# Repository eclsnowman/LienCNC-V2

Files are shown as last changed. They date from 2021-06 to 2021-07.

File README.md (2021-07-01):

# LienCNC-V2
My Design for a Heavy Duty CNC Router

LienCNC V2 Render1

Hello and welcome to my Github for the LienCNC V2, which is a CNC router I designed as an upgrade to my previous CNC Router. I completed this new router design and build during December of 2020. The previous router I used was the R7 CNC which was a project I helped develop with my friend Brandon who owned SMW3D/HobbyFab. The R7 CNC was a great machine and cut all the aluminum parts required to build my new machine. The majority of the work I do on my router is cutting aluminum, so I wanted something with higher stiffness, higher mass for dampening vibrations, and all around overbuilt just how I like it.

The performance of this new machine checks all the boxes I had hoped for during my time in Solidworks designing the upgrade. The major specifications for this CNC design are as follows:

***Construction:*** 8020 Aluminum Profiles and ½” ATP-5 Cast tooling plates  
***Motion:*** RM1605 (5mm pitch) Ball Screws, HGR20 Linear Rails, Nema24 3Nm Closed Loop Steppers  
***Spindle:*** 2.2KW ER20 220V 24000RPM Spindle  
***Controls:*** Minisforum UM300 MiniPC into CNCDrive AXBB-E Controller w/ UCSB Breakout  
***Software:*** CNCDrive UCCNC 1.2113  
***Power Supplies:*** 48V/20A Main PSU, 24V/2.5A PSU, 5V10A PSU, 48V-to-12V 5A Buck Converter  
***Machine Travel:*** X=738mm  /  Y=724.5mm  /  Z=129mm  
***Max Speed:*** X=8,000mm/min  /  Y=10,000mm/min  /  Z = 8,000mm/min  

In the files I have on this Github are all my native Solidworks 2018 design files, as well as those files converted into many other 3D formats including; Fusion360, Step, Iges, Etc. In addition, I have included PDF, DXF, and DWG prints for all the major fabricated components and assemblies. The manuals for all the components that I referenced for configuring my build are also included. Lastly I have included my UCCNC configuration *.pro” file. 

The only item I have not included is a wiring diagram. Unfortunately the time it would take to make a wiring diagram to the caliber I could feel proud of is just not something I have time for right now. Building a CNC requires a fairly ample back catalog of knowledge to take on. If the wiring of a project like using the electrical manuals is not something you feel comfortable with, then seeking advice from an expert on your project would be advised. That being said I have included pictures and 3D models of my electrical cabinet design that you could use as reference on your own project.

I hope the files, resources, pictures, and designs I have provided here can help you if you decide to take on this project. And if you don’t build this design, I hope these resources can act as a jumping off point for your own project.

If you find any errors that I should correct please feel free to submit a pull request with the changes, or submit an issue and I will do my best to correct the problem as time allows.

Happy Making,
– Eric Lien

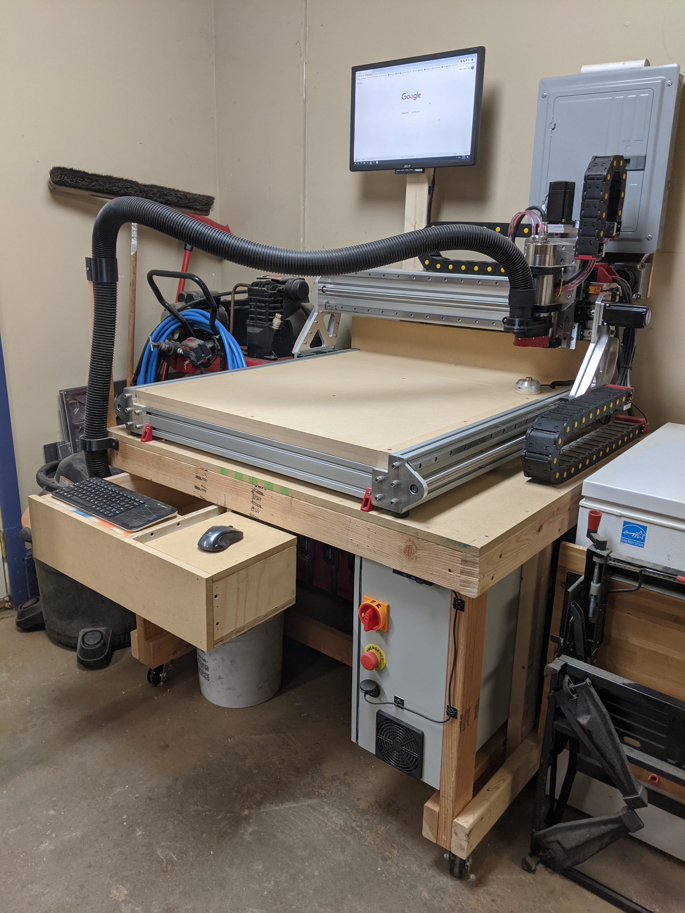
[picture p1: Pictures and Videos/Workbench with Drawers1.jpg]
LienCNC V2 Finished

LienCNC V2 Render2

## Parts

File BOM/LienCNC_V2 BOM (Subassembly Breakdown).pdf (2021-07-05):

LienCNC V2

ITEM NO.

QTY. By
| Assembly | PART NUMBER | DESCRIPTION | Prints & Manuals
1 | 1 | CNC Base and Electronics | Assembly | LCNC_BC & LCNC_TLA
1.1 | 1 | Workbench | Wood | LCNC_WB
1.1.1 | 1 | 2x4 Frame | Lumber Frame | LCNC_WB
1.1.1.1 | 654 in | 2x4 (Pine) | 2x4 Lumber (1.5" x 3.5") | LCNC_WB
1.1.2 | 1 | Workbench Lower Shelf | 3/4" Plywood or MDF | LCNC_WB
1.1.3 | 1 | Workbench Top | 3/4" Plywood or MDF | LCNC_WB
1.1.4 | 2 | 2406T34 | Ridged Caster | LCNC_WB
1.1.5 | 2 | 2406T29 | Swivel Caster | LCNC_WB
1.1.6 | 1 | Shelf Back Panel | 3/4" Plywood or MDF | LCNC_WB
1.1.7 | 16 | 92351A544 | 1/4" x 1-1/4"L Lag | LCNC_WB
1.2 | 1 | LienCNC_Base | CNC Base Frame | LCNC_BA
1.2.1 | 1 | 8020_Base_Frame | 8020 Aluminum Frame Components | LCNC_BF
1.2.1.1 | 2 | 40-4012 (1000mm) | 80/20 40-4012 PROFILE | LCNC_BF
1.2.1.2 | 4 | 40-4080 (860mm) | 80/20 40-4080 PROFILE | LCNC_BF
1.2.2 | 1 | Spoilboard (Bottom) | 3/4" MDF Bottom Spoilboard | LCNC_BA
1.2.3 | 1 | Spoilboard (Top) | 3/4" MDF Top Spoilboard | LCNC_BA
1.2.4 | 36 | 98689A116 | 8mm SST Washer | LCNC_BA
1.2.5 | 16 | 91292A208 | SCS M8 x 1.25 x 45mm Long PT (SST) | LCNC_BA
1.2.6 | 20 | 8mm SCS SST x 25mm | Stainless Steel M8 Socket Head Cap Screw | LCNC_BA
1.2.7 | 4 | 40-2849 (8020 Foot) | 8020 Rubber Foot | LCNC_BA
1.2.8 | 8 | 40-1984 | M8 Tnut for 40 series Tslot | LCNC_BA
1.2.9 | 16 | 5mm SCS SST x 12mm | M5 SCS | LCNC_BA
1.2.10 | 16 | 98689A114 | 5mm SST Washer | LCNC_BA
1.2.11 | 16 | M5_Tnut_40Series-Profile | M5 Tnut for 40 series Tslot | LCNC_BA
1.2.12 | 1 | Y_Axis_Endplate | Front Right Y Axis Endplate | LCNC_YE & LCNC_BA
1.2.13 | 2 | Nema24_Yaxis_Endplate | Fabricated Plate | LCNC_YE & LCNC_BA
1.2.14 | 2 | Backsplash | 1/8" Aluminum Dust Backsplash | LCNC_DG & LCNC_BA
1.2.15 | 2 | Side Profiles | Fabricated Angle Aluminum Side Dust Profiles | LCNC_DG & LCNC_BA
1.2.16 | 1 | MirrorY_Axis_Endplate | Fabricated Plate | LCNC_YE & LCNC_BA
1.3 | 1 | CNC Control Panel | Electrical CNC Controls | LCNC_CP & LCNC_BC
1.3.1 | 1 | YuCo YC-20X16X10-UL | 16x20x10 Yuco Electronics Enclosure | LCNC_CP
1.3.2 | 1 | SCN-1000-48 | 48V/20A Switching CNC Power supply | LCNC_CP
1.3.3 | 1 | MEAN WELL MDR 24V | MEAN WELL MDR-60-24 DIN-Rail Power Supply 24V 2.5 Amp 60W | LCNC_CP
1.3.4 | 1 | MEAN WELL MDR 5V | MEAN WELL MDR-60-5 AC to DC DIN-Rail Power Supply 5V 10 Amp 50W | LCNC_CP
1.3.5 | 1 | CNCDRIVE AXBB-E | AXBB-E Ethernet Motion Controller + UCCNC License File Bundle) | LCNC_CP
1.3.6 | 1 | CNCDIVE UCSB | UCSB single port breakout board for AXBB-E | LCNC_CP
1.3.7 | 1 | CNCDrive_Parts_Mount | 3D Printed Part | LCNC_CP & STLs
1.3.8 | 4 | CL57Y Stepper Driver | YE Series 1 Axis Closed Loop Stepper CNC Kit 3.0 Nm(424.92oz.in) Nema 24
| | | Motor & Driver | LCNC_CP
1.3.9 | 1 | 7578K262 | Slotted Wire Duct with Snap-on Cover Adhesive-Back, 2-1/4" Ht X 1-1/2" Wd, 3-
| | | 1/4'Lg, Gray | LCNC_CP
1.3.10 | 1 | 8961K150 | Steel DIN 3 Rail, 7.5mm Deep | LCNC_CP
1.3.14 | 2 | Lovato Electric FB01F1P | DIN Rail Mounted Midget Fuse Holder, 2 Pole, 18 to 8 AWG, 30 Amp, 600V | LCNC_CP
1.3.15 | 10 | 7641K526 | AKA 7641K52 = Screw Terminal DIN-Rail Terminal Block (8-22 ga) | LCNC_CP
1.3.16 | 2 | 7641K350 | Din Rail Mounted End Stop | LCNC_CP
1.3.17 | 4 | 7641K924 | AKA 7641K921 = Screw Terminal DIN-Rail Terminal Block (12-22 ga) | LCNC_CP
1.3.18 | 18 | M5 Bolt Nut Washer Assembly | Assembly | LCNC_CP
1.3.18.1 | 18 x 1 | 5mm x 12mm SST BSC | 5mm x 10mm SST BSC | LCNC_CP
1.3.18.2 | 18 x 1 | M5 Nylock Nut | Trimcraft M5 Nylock Nut | LCNC_CP
1.3.18.3 | 18 x 2 | M5 Flat Washer | Trimcraft M5 Flat Washer | LCNC_CP
1.3.19 | 1 | MinixForum_UM300 | Mini PC for running UCCNC | LCNC_CP
1.3.20 | 1 | Power Brick Mount | 3D Printed Part | LCNC_CP & STLs
1.3.21 | 1 | UM300 Power Brick | Part of UM300 | LCNC_CP
1.3.22 | 1 | 120mm Fan | 120mm (48V) fan | LCNC_CP
1.3.23 | 2 | 120mm Filter | 120mm filter for air inlet and outlet | LCNC_CP
1.3.24 | 1 | ALLEN-BRADLEY_194E-E25-1753-6N | Main Disconnect | LCNC_CP
1.3.25 | 1 | YW1B-V4E11R EMERGENCY STOP (IDEC) | Estop (one NO one NC contact) | LCNC_CP
1.3.26 | 1 | Gland Plate Assembly | Assembly | LCNC_CP
1.3.26.1 | 1 | Controller Gland Plate | Fabricated Plate | LCNC_CP
1.3.26.2 | 5 | GX20-4 Aviation Connector | 20mm 4 pin panel connection (Stepper Coils and 12V Power) | LCNC_CP
1.3.26.3 | 5 | GX12-3 Aviation Connector | 12mm 3 pin panel connection (Limit Switches and Tool Probe)) | LCNC_CP
1.3.26.4 | 4 | GX16-6 Aviation Connector | 20mm 4 pin panel connection (Encoder Connections) | LCNC_CP
1.3.26.5 | 2 | Female US 3 Pin Power Socket Plug Panel Mount | US 3 Pin Power Plugs for external VAC and Aux Plugs | LCNC_CP
1.3.26.6 | 1 | CNLINKO LP24 4pin Connector | 4 Pin Plug Disconnect for VFD Power to Spindle | LCNC_CP
1.3.26.7 | 1 | BATIGE USB3_HDMI_Panel_Mount | Panel mount HDMI out to Monitor | LCNC_CP
1.3.26.8 | 1 | 3/4 Knockout Cord Grip | 3/4" Knockout Cord Grip for Controller Power In | LCNC_CP
1.3.27 | 1 | IceSpring_USB3_X2_Panel_Mount | Panel Mount USB for Front Connection to Mini PC | LCNC_CP
1.3.28 | 1 | GT-2R2G-2 (220V) Huanyang VFD | HUANYANG - 2.2KW 220V AC Vector Control VFD With Modbus | LCNC_CP
1.3.29 | 1 | AD-SSR630-22-DCZ | 30A SSR Relay | LCNC_CP
1.3.30 | 1 | AD-SSR210-22-DCZ | 10A SSR Relay | LCNC_CP
1.4 | 4 | 92351A544 | 1/4" x 1-1/4"L Lag | LCNC_BC
1.5 | 4 | 92141A029 | 1/4" Flat Washer | LCNC_BC
2 | 1 | X Axis ASMB | Assembly | LCNC_XA & LCNC_TLA
2.1 | 1 | X Axis_Beam | Assembly | LCNC_XA
2.1.1 | 1 | 40-8016 (1000mm) | 80/20 40-8016 PROFILE | LCNC_XB & LCNC_XA
2.2 | 2 | HGR20 LINEAR GUIDE SUBASSEMBLY | Assembly | LCNC_XA
2.2.1 | 1 x 2 | HGR20R x 1000 mm | 20mm Linear Rail | LCNC_XA
2.2.2 | 2 x 2 | HGH20CAZ0C | 20mm Linear Rail Block | LCNC_XA
2.2.2.3 | 2 x 1 | 2421K31 | M6 x1 Low Profile Zerk | LCNC_XA
2.2.3 | 17 | M5_Rail_Mounting-Tnut_ASMB | Assembly | LCNC_XA
2.2.3.1 | 17 x 1 | 5mm SCS SST x 20mm | M5 SCS | LCNC_XA
2.2.3.2 | 17 x 1 | 98689A114 | M5 Compact Washer | LCNC_XA
2.2.3.3 | 17 x 1 | M5_Tnut_40Series-Profile | M5 Tnut for 40 series Tslot | LCNC_XA
2.3 | 1 | Endstop_With_Mount(X_Y) | Assembly | LCNC_XA
2.3.1 | 1 | Endstop Rail Mount | 3D Printed Part | LCNC_XA & STLs
2.3.2 | 1 | TL-W5MC1 | Inductive Probe(NO NPN) | LCNC_XA
2.3.3 | 2 | M3 SCS SST x 10mm | M3 SCS | LCNC_XA
2.4 | 1 | Spindle Cooling Radiator System | Assembly | LCNC_SR
2.4.1 | 1 | XSPC EX240 Radiator | 240mm Radiator | LCNC_SR
2.4.2 | 2 | Noctua_nf-p12 redux-1700 | 20mm Fan (12V) | LCNC_SR
2.4.3 | 1 | Freezemod FS6PD-17 Pump and Resevoive combo | Freezemod Pump/Reservoir | LCNC_SR

See print LCNC_OV for full assembly overview

2.4.3.2 | 1 | Freezemod PU-FS6M Bracket | Fabricated Plate | LCNC_DG & LCNC_SR
2.4.3.3 | 1 | Bitspower_T_Fitting | G14 T-Fitting | LCNC_SR
2.4.3.4 | 2 | EK-AF Extender Rotary M-M G1_4 | G14 MxM Swivel Union | LCNC_SR
2.4.3.5 | 2 | EK-AF Angled 90deg G1_4 | G14 MxF Swivel 90deg Elbow | LCNC_SR
2.4.3.6 | 2 | G14x6mm_Barb | G14 Male x 6mm Barb Fitting | LCNC_SR
2.4.3.7 | 1 | G14_Valve | Válvula Bitspower Roscas 1/4" | LCNC_SR
2.4.3.8 | 1 | G14_Plug | G14 Plug (Acetal) | LCNC_SR
2.4.4 | 2 | G14x6mm_Barb | G14 Male x 6mm Barb Fitting | LCNC_SR
2.4.5 | 1 | Flow_Temp_Indicator_ASMB | Assembly | LCNC_SR
2.4.5.1 | 1 | Flow and Temp Printed Mount | 3D Printed Part | LCNC_SR & STLs
2.4.5.2 | 1 | Fosa Pointer Temp Display | Digital Temp Indicator | LCNC_SR
2.4.5.3 | 1 | Fosa G14 Flow Meter | Acrylic Flow Wheel Indicator | LCNC_SR
2.4.5.4 | 1 | EK-AF Angled 90deg G1_4 | G14 MxF Swivel 90deg Elbow | LCNC_SR
2.4.5.5 | 2 | G14x6mm_Barb | G14 Male x 6mm Barb Fitting | LCNC_SR
2.4.6 | 1 | EK-AF Angled 90deg G1_4 | G14 MxF Swivel 90deg Elbow | LCNC_SR
2.4.7 | 1 | Water Cooling Tubes | 5mm ID x 8mm OD Clear Tube | LCNC_SR
2.4.8 | 2 | G14_Plug | G14 Plug (Acetal) | LCNC_SR
2.4.9 | 1 | Radiator Mount1 | 3D Printed Part | LCNC_SR & STLs
2.4.10 | 1 | Radiator Mount2 | 3D Printed Part | LCNC_SR & STLs
2.4.11 | 2 | Fan_Grill | 3D Printed Part | LCNC_SR & STLs
2.4.12 | 4 | 3mm x 06mm SST BSC | 3mm x 6mm SST BSC | LCNC_SR
2.4.13 | 8 | 3mm x 30mm SST BSC | 3mm x 30mm SST BSC | LCNC_SR
2.4.14 | 6 | 5mm SCS SST x 16mm | M5 SCS | LCNC_SR
2.4.15 | 8 | 98689A114 | 5mm SST Washer | LCNC_SR
2.4.16 | 8 | M5_Tnut_40Series-Profile | M5 Tnut for 40 series Tslot | LCNC_SR
2.4.17 | 2 | 5mm SCS SST x 25mm | M5 SCS | LCNC_SR
2.4.18 | 4 | 4mm SCS SST x 08mm | M4 SCS | LCNC_SR
2.4.19 | 4 | 98689A113 | 4mm SST Washer | LCNC_SR
2.5 | 1 | XandY Axis Ballscrew ASMB | Assembly | LCNC_XA
2.5.1 | 4 | 5mm SCS SST x 25mm | M5 SCS | LCNC_XA
2.5.2 | 10 | 98689A114 | 5mm SST Washer | LCNC_XA
2.5.3 | 4 | 91290A207 | M6 BO FT SCS x 60mm | LCNC_XA
2.5.4 | 4 | 98689A115 | 6mm SST Washer | LCNC_XA
2.5.5 | 1 | Nema24_Spacer_Plate | Fabricated Plate | LCNC_MP2 & LCNC_XA
2.5.6 | 1 | 24HE34-5004D-E1000 | Nema 24 - 3Nm CL Stepper | LCNC_XA
2.5.7 | 1 | SFU1605-1610_Ball-Nut-Housing | 16mm Ball Screw Nut Housing | LCNC_XA
2.5.8 | 1 | RM1605-C7 L1000_Overall | 16mm Ball Screw x 1000mm L | LCNC_XA
2.5.9 | 1 | SFU1605-3 | 16mm Ball Screw Nut | LCNC_XA
2.5.10 | 1 | BK12 | 12mm Fixed Side Bearing Block | LCNC_XA
2.5.11 | 1 | Shaft Coupling (3 piece) | 10mm x 10 mm Shaft Coupling | LCNC_XA
2.5.11.1 | 2 | 9939T321 | Set Screw Vibration-Damping Precision Flexible Shaft Couplings | LCNC_XA
2.5.11.2 | 1 | 9845T14 | Urethane Flex Shaft Spider | LCNC_XA
2.5.12 | 1 | 6661K83 | 6000-2RS (10x26x8 Sealed Bearing) | LCNC_XA
2.5.13 | 6 | 5mm x 20mm SST BSC | 5mm x 10mm SST BSC | LCNC_XA
3 | 1 | Y Axis ASMB | Assembly | LCNC_YR
3.1 | 1 | Gantry_Riser | Fabricated Plate | LCNC_GP1 & LCNC_YR
3.2 | 1 | Y-Axis_Ballscrew_Connection_Plate | Fabricated Plate | LCNC_MP2 & LCNC_YR
3.3 | 1 | Gantry Rib1 | Fabricated Plate | LCNC_GR & LCNC_YR
3.4 | 1 | Gantry Rib2 | Fabricated Plate | LCNC_GR & LCNC_YR
3.5 | 1 | Drag Chain Mount (Y Axis) | Fabricated Plate | LCNC_MP2 & LCNC_YR
3.6 | 1 | Endstop_With_Mount(X_Y) | Assembly | LCNC_YR
3.6.1 | 1 | Endstop Rail Mount | 3D Printed Part | LCNC_YR & STLs
3.6.2 | 1 | TL-W5MC1 | Inductive Probe(NO NPN) | LCNC_YR
3.6.3 | 2 | M3 SCS SST x 10mm | M3 SCS | LCNC_YR
3.7 | 1 | 91290A238 | 5mm BO SCS x 18mm | LCNC_YR
3.8 | 1 | 91828A241 | M5 Hex Nut | LCNC_YR
3.9 | 8 | M8 SCS SST x 30mm | M8 SCS | LCNC_YR
3.10 | 8 | 98689A116 | 8mm SST Washer | LCNC_YR
3.11 | 19 | 5mm SCS SST x 20mm | M5 SCS | LCNC_YR
3.12 | 27 | 98689A114 | 5mm SST Washer | LCNC_YR
3.13 | 4 | 5mm SCS SST x 25mm | M5 SCS | LCNC_YR
3.14 | 4 | 5mm SCS SST x 12mm | M5 SCS | LCNC_YR
3.15 | 1 | HGR20 LINEAR GUIDE SUBASSEMBLY | Assembly | LCNC_YR
3.15.1 | 1 | HGR20R x 1000 mm | 20mm Linear Rail | LCNC_YR
3.15.2 | 2 | HGH20CAZ0C | 20mm Linear Rail Block | LCNC_YR
3.15.2.3 | 1 | 2421K31 | M6 x1 Low Profile Zerk | LCNC_YR
3.15.3 | 17 | M5_Rail_Mounting-Tnut_ASMB | Assembly | LCNC_YR
3.15.3.1 | 17 x 1 | 5mm SCS SST x 20mm | M5 SCS | LCNC_YR
3.15.3.2 | 17 x 1 | 98689A114 | M5 Compact Washer | LCNC_YR
3.15.3.3 | 17 x 1 | M5_Tnut_40Series-Profile | M5 Tnut for 40 series Tslot | LCNC_YR
4 | 2 | XandY Axis Ballscrew ASMB | Assembly (2 x One for each Y Axis) | LCNC_YR
4.1 | 2 x 4 | 5mm SCS SST x 25mm | M5 SCS | LCNC_YR
4.2 | 2 x 10 | 98689A114 | 5mm SST Washer | LCNC_YR
4.3 | 2 x 4 | 91290A207 | M6 BO FT SCS x 60mm | LCNC_YR
4.4 | 2 x 4 | 98689A115 | 6mm SST Washer | LCNC_YR
4.5 | 2 x 1 | Nema24_Spacer_Plate | Fabricated Plate | LCNC_MP2 & LCNC_YR
4.6 | 2 x 1 | 24HE34-5004D-E1000 | Nema 24 - 3Nm CL Stepper | LCNC_YR
4.7 | 2 x 1 | SFU1605-1610_Ball-Nut-Housing | 16mm Ball Screw Nut Housing | LCNC_YR
4.8 | 2 x 1 | RM1605-C7 L1000_Overall | | LCNC_YR
4.9 | 2 x 1 | SFU1605-3 | 16mm Ball Screw Nut | LCNC_YR
4.10 | 2 x 1 | BK12 | 12mm Fixed Side Bearing Block | LCNC_YR
4.11 | 2 x 1 | Shaft Coupling (3 piece) | 10mm x 10 mm Shaft Coupling | LCNC_YR
4.11.1 | 2 x 2 | 9939T321 | Set Screw Vibration-Damping Precision Flexible Shaft Couplings | LCNC_XA
4.11.2 | 2 x 1 | 9845T14 | Urethane Flex Shaft Spider | LCNC_YR
4.12 | 2 x 1 | 6661K83 | 6000-2RS (10x26x8 Sealed Bearing) | LCNC_YR
4.13 | 2 x 6 | 5mm x 20mm SST BSC | 5mm x 10mm SST BSC | LCNC_YR
5 | 1 | Y Axis ASMB (Mirror) | Assembly | LCNC_YL
5.1 | 1 | Y-Axis_Ballscrew_Connection_Plate | Fabricated Plate | LCNC_MP2 & LCNC_YL
5.2 | 1 | Gantry Rib1 | Fabricated Plate | LCNC_GR & LCNC_YR
5.3 | 1 | Gantry Rib2 | Fabricated Plate | LCNC_GR & LCNC_YR
5.4 | 1 | MirrorGantry_Riser | Fabricated Plate | LCNC_GP2 & LCNC_YL
5.5 | 1 | Endstop_With_Mount(X_Y) | Assembly | LCNC_YL
5.5.1 | 1 | Endstop Rail Mount | 3D Printed Part | LCNC_YL & STLs
5.5.2 | 1 | TL-W5MC1 | Inductive Probe(NO NPN) | LCNC_YL

5.5.3 | 2 | M3 SCS SST x 10mm | M3 SCS | LCNC_YL
5.6 | 1 | 91290A238 | 5mm BO SCS x 18mm | LCNC_YL
5.7 | 1 | 91828A241 | M5 Hex Nut | LCNC_YL
5.8 | 8 | M8 SCS SST x 30mm | M8 SCS | LCNC_YL
5.9 | 8 | 98689A116 | 8mm SST Washer | LCNC_YL
5.1 | 16 | 5mm SCS SST x 20mm | M5 SCS | LCNC_YL
5.11 | 24 | 98689A114 | 5mm SST Washer | LCNC_YL
5.12 | 4 | 5mm SCS SST x 25mm | M5 SCS | LCNC_YL
5.13 | 4 | 5mm SCS SST x 12mm | M5 SCS | LCNC_YL
5.14 | 1 | HGR20 LINEAR GUIDE SUBASSEMBLY | Assembly | LCNC_YL
5.14.1 | 1 | HGR20R x 1000 mm | 20mm Linear Rail | LCNC_YL
5.14.2 | 2 | HGH20CAZ0C | 20mm Linear Rail Block | LCNC_YL
5.14.2.3 | 1 | 2421K31 | M6 x1 Low Profile Zerk | LCNC_YL
5.14.3 | 17 | M5_Rail_Mounting-Tnut_ASMB | Assembly | LCNC_YL
5.14.3.1 | 17 x 1 | 5mm SCS SST x 20mm | M5 SCS | LCNC_YL
5.14.3.2 | 17 x 1 | 98689A114 | M5 Compact Washer | LCNC_YL
5.14.3.3 | 17 x 1 | M5_Tnut_40Series-Profile | M5 Tnut for 40 series Tslot | LCNC_YL
6 | 1 | Z Axis ASMB | Assembly | LCNC_YL
6.1 | 1 | HY02D223B | 2.2KW - 24000RPM HUANYANG Spindle | LCNC_ZA & Huanyang 2.2KW Spindle.pdf
6.2 | 2 | YY-M-15 80mm | 80mm Spindle Clamp | LCNC_ZA
6.3 | 1 | Endmill | Endmill for representation purposes | LCNC_ZA
6.4 | 1 | TL-W5MC1 | Inductive Probe(NO NPN) | LCNC_ZA
6.5 | 1 | 24HE34-5004D-E1000 | Nema 24 - 3Nm CL Stepper | LCNC_ZA
6.6 | 1 | Banana Plug Socket (Black) | Black Z Probe Plug | LCNC_ZA
6.7 | 1 | Banana Plug Socket (Red) | Red Z Probe Plug | LCNC_ZA
6.8 | 2 | HGR20-300mm w/ 2xBlocks | 20mm x 300L Linear Rail w/ Bearings | LCNC_ZA
6.8.1 | 1 | HGR20R LINEAR GUIDE RAIL, CONFIGURABLE | 20mm Linear Rail | LCNC_ZA
6.8.2 | 2 | HGH20CAZ0C | 20mm Linear Rail Block | LCNC_ZA
6.8.2.3 | 1 | 2421K31 | M6 x1 Low Profile Zerk | LCNC_ZA
6.9 | 1 | BF12 | 12mm Support Side Bearing Block | LCNC_ZA
6.1 | 1 | BK12 | 12mm Fixed Side Bearing Block | LCNC_ZA
6.11 | 1 | RM1605-C7 L300_Overall | 16mm x 300mm Ballscrew | LCNC_ZA
6.12 | 1 | SFU1605-1610_Ball-Nut-Housing | 16mm Ball Screw Nut Housing | LCNC_ZA
6.13 | 1 | SFU1605-3 | 16mm Ball Screw Nut | LCNC_ZA
6.14 | 1 | Shaft Coupling (3 piece) | 10mm x 10 mm Shaft Coupling | LCNC_ZA
6.14.1 | 2 | 9939T321 | Set Screw Vibration-Damping Precision Flexible Shaft Couplings | LCNC_ZA
6.14.2 | 1 | 9845T14 | Urethane Flex Shaft Spider | LCNC_ZA
6.15 | 1 | Drag Chain Mount (Z Axis) | Fabricated Plate | LCNC_MP1 & LCNC_ZA
6.16 | 1 | Z_Axis_Motor_Plate | Fabricated Plate | LCNC_MP1 & LCNC_ZA
6.17 | 1 | Z_Axis_Plate | Fabricated Plate | LCNC_SP & LCNC_ZA
6.18 | 1 | Z_Axis_Spacer | Fabricated Plate | LCNC_MP1 & LCNC_ZA
6.19 | 1 | Z_Axis_Spacer_DC | Fabricated Plate | LCNC_MP2 & LCNC_ZA
6.2 | 1 | X_Axis_Plate | Fabricated Plate | LCNC_XP & LCNC_ZA
6.21 | 1 | X-Axis_Ballscrew_Connection_Plate | Fabricated Plate | LCNC_MP2 & LCNC_ZA
6.22 | 1 | Nema24_Spacer_Plate | Fabricated Plate | LCNC_MP2 & LCNC_ZA
6.23 | 1 | Drag Chain Mount (X Axis) | Fabricated Plate | LCNC_MP1 & LCNC_ZA
6.24 | 1 | Z_Axis_Endstop_Mount | 3D Printed Part | LCNC_ZA & STLs
6.25 | 1 | Spindle Probe Jack Mount | 3D Printed Part | LCNC_ZA & STLs
6.26 | 1 | 91290A238 | 5mm BO SCS x 18mm | LCNC_ZA
6.27 | 2 | 91828A241 | M5 Hex Nut | LCNC_ZA
6.28 | 26 | 5mm SCS SST x 25mm | M5 SCS | LCNC_ZA
6.29 | 81 | 98689A114 | 5mm SST Washer | LCNC_ZA
6.3 | 24 | 5mm SCS SST x 16mm | M5 SCS | LCNC_ZA
6.31 | 17 | 5mm SCS SST x 20mm | M5 SCS | LCNC_ZA
6.32 | 1 | 91290A194 | 5mm BO SCS x 30mm | LCNC_ZA
6.33 | 8 | 5mm SCS SST x 14mm | M5 SCS | LCNC_ZA
6.34 | 6 | M6 SCS BO PT x 40mm | 6mm BO PT SCS x 40mm | LCNC_ZA
6.35 | 6 | 98689A115 | 6mm SST Washer | LCNC_ZA
6.36 | 4 | 5mm SCS SST x 30mm | M5 SCS | LCNC_ZA
6.37 | 3 | 3mm x 10mm SST BSC | 3mm x 10mm SST BSC | LCNC_ZA
6.38 | 2 | 5mm x 10mm SST BSC | 5mm x 10mm SST BSC | LCNC_ZA
6.39 | 2 | 3mm x 16mm SST SCS | 3mm x 16mm SST SCS | LCNC_ZA
6.4 | 2 | 3mm x 12mm SST SCS | 3mm x 12mm SST SCS | LCNC_ZA
7 | 1 | X Axis Drag Chain ASMB | Assembly | LCNC_DC & LCNC_TLA
7.1 | 1 | Cable Chain X End Mount | 3D Printed Part | STLs
7.2 | 1 | Cable Chain Exit Combs V2 | 3D Printed Part | STLs
7.3 | 1 | Cable Chain Exit Combs | 3D Printed Part | STLs
7.4 | 1 | H25 (25x57mm Drag Chain) | Assembly | LCNC_DC
7.4.1 | 1 | H25-EndLink1 (25x57_ID_Drag_Chain) | Link1 | LCNC_DC
7.4.2 | 25 | H25-CenterLink (25x57_ID_Drag_Chain) | Link2 | LCNC_DC
7.4.3 | 1 | H25-EndLink2 (25x57_ID_Drag_Chain) | Link3 | LCNC_DC
7.5 | 8 | 5mm x 12mm SST BSC | 5mm x 10mm SST BSC | LCNC_DC
7.6 | 4 | 5mm x 10mm SST BSC | 5mm x 10mm SST BSC | LCNC_DC
7.7 | 6 | 5mm x 16mm SST BSC | 5mm x 10mm SST BSC | LCNC_DC
7.8 | 4 | 90225A101 | M5 Square Nut | LCNC_DC
7.9 | 2 | M5_Tnut_40Series-Profile | M5 Tnut for 40 series Tslot | LCNC_DC
7.1 | 2 | 98689A114 | 5mm SST Washer | LCNC_DC
8 | 1 | Z Axis Drag Chain ASMB | Assembly | LCNC_DC & LCNC_TLA
8.1 | 1 | H25 (25x38mm Drag Chain) | Assembly | LCNC_DC
8.1.1 | 1 | H25-EndLink1 (25x38_ID_Drag_Chain) | Link1 | LCNC_DC
8.1.2 | 10 | H25-CenterLink (25x38_ID_Drag_Chain) | Link2 | LCNC_DC
8.1.3 | 1 | H25-EndLink2 (25x38_ID_Drag_Chain) | Link3 | LCNC_DC
8.2 | 1 | Cable Chain Exit Combs Z1 | 3D Printed Part | STLs
8.3 | 1 | Cable Chain Exit Combs Z1 | 3D Printed Part | STLs
8.4 | 8 | 5mm x 16mm SST BSC | 5mm x 10mm SST BSC | LCNC_DC
8.5 | 8 | 90225A101 | M5 Square Nut | LCNC_DC
8.6 | 8 | 5mm x 12mm SST BSC | 5mm x 10mm SST BSC | LCNC_DC
9 | 1 | Y Axis Dragchain | Assembly | LCNC_DC & LCNC_TLA
9.1 | 1 | Cable Chain Exit Comb Y Exit V3 | 3D Printed Part | STLs
9.2 | 1 | Cable Chain X End Mount | 3D Printed Part | STLs
9.3 | 1 | Cable Chain Exit Comb Y Exit | 3D Printed Part | STLs
9.4 | 1 | H25 (25x57mm Drag Chain) | Assembly | LCNC_DC
9.4.1 | 1 | H25-EndLink1 (25x57_ID_Drag_Chain) | Link1 | LCNC_DC
9.4.2 | 25 | H25-CenterLink (25x57_ID_Drag_Chain) | Link2 | LCNC_DC

9.4.3

| 1 | H25-EndLink2 (25x57_ID_Drag_Chain) | Link3 | LCNC_DC
9.5 | 4 | 90225A101 | M5 Square Nut | LCNC_DC
9.6 | 4 | 5mm x 20mm SST BSC | 5mm x 10mm SST BSC | LCNC_DC
9.7 | 8 | 5mm x 12mm SST BSC | 5mm x 10mm SST BSC | LCNC_DC
9.8 | 4 | 5mm x 10mm SST BSC | 5mm x 10mm SST BSC | LCNC_DC
9.9 | 2 | 90305A112 | Wood Screw | LCNC_DC
10 | 1 | Dust_Shoe | Assembly | LCNC_DU
10.1 | 1 | Dust_Shoe | 3D Printed Part | LCNC_DU & STLs
10.2 | 8 | 3mm x 06mm SST BSC | 3mm x 6mm SST BSC | LCNC_DU
10.3 | 2 | 5mm SCS SST x 20mm | M5 SCS | LCNC_DU
10.4 | 2 | 98689A114 | 5mm SST Washer | LCNC_DU
10.5 | 2 | M5 Nylock Nut | Trimcraft M5 Nylock Nut | LCNC_DU
10.6 | 20 | 8mm x 3mm Neodymium Magnet | Magnets to hold on dust shoe | LCNC_DU
11 | 1 | 5Gallon_Pail_Dust_Cyclone | Assembly | LCNC_DU
11.1 | 1 | 5_Gallon_Pail | Cut down 5gal pail to act as upper section | LCNC_DU
11.2 | 1 | 5_Gallon_Pail | 5gal pail | LCNC_DU
11.3 | 1 | Cyclone_Top_Under_Plate | Fabricated Wood Plate | LCNC_DU
11.4 | 1 | 2in x 6in Length of PVC Pipe | 6in Length of PVC Pipe | LCNC_DU
11.5 | 2 | 4880K26 | 2in PVC FxF Elbow | LCNC_DU
11.6 | 1 | 2in x 1.75in Length of PVC Pipe | 1.75in Length of PVC Pipe | LCNC_DU
11.7 | 1 | 1608T103 | 2in PVC FxF Union | LCNC_DU
11.8 | 2 | 2IN_ABS_Coupling | 2IN_ABS_Coupling | LCNC_DU
11.9 | 1 | 1608T125 | 2in PVC FxF Elbow | LCNC_DU
11.1 | 1 | Cyclone_Baffle_Plate | Fabricated Wood Plate | LCNC_DU
11.11 | 4 | 90630A121 | 3/8" Nylock Nut | LCNC_DU
11.12 | 4 | 98023A031 | 3/8" Washer | LCNC_DU
11.13 | 1 | 95475A646 | 3/8 Threaded Rod | LCNC_DU
11.14 | 2 | 2IN_Pipe_to_2.25ID_Hose_Adapter | 3D Printed Part | LCNC_DU & STLs

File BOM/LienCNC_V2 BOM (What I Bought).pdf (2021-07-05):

LienCNC V2 Parts List | *Note, these are the parts I purchased. There are other items I had that other users might need to buy misc metric hardware, crimp wire ferruls, metric taps, misc interconnection wiring in control panel, etc.
Vendor | Qty: | PN / EAN# / ASIN# | Price (Ea) | Price (Total) | Description | Notes | Link
Amazon | 1 | HGR20-300 | $78.00 | $78.00 | Linear Guide Rail 2Pcs HGR20-300mm, Linear Slide Rail with 1Pcs RM1605-300mm Ballscrew with BF12/BK12 Kit Linear Slide Rail Guide Rail Square for DIY CNC Routers Lathes Mills | Note, my rail lengths were slightly over sized and ball screws were slightly off print. So I had to machine relief pockets in my plates for oversided rails and made 3DP spacers at the end of the ball screws to go between 6900-RS bearings and ball screw shoulders. | https://www.amazon.com/gp/product/B083CKZR5K/ref=ppx_y

o_dt_b_asin_title_o02_s00?ie=UTF8&psc=1 (https://www.amazon.com/gp/product/B083CKZR5K/ref=ppx_yo_dt_b_asin_title_o02_s00?ie=UTF8&psc=1)

Amazon | 3 | HGR20-1000 | $107.99 | $323.97

Linear Guide Rail 2Pcs HGR20-1000mm Linear Slide Rail with 1Pcs RM1605-1000mm Ballscrew with BF12/BK12 Kit Linear Slide Rail Guide Rail Square for DIY CNC Routers Lathes Mills. Note that since the design only uses 1 leanr rail per Y axis, you could just buy a seperate matching ball screw which means you only need 2 of these kits. But I didn't want any mismatch on the components, so now I just have 2 extra rails and 4 extra carriages as future spares.

Note, my rail lengths were slightly over sized and ball screws were slightly off
print. So I had to machine relief pockets in my plates for oversided rails and
made 3DP spacers at the
end of the ball screws to go between 6900-RS bearings
and ball screw shoulders.

https://www.amazon.com/gp/product/B083CKZR5K/ref=ppx_yo_dt_b_asin_title_o02_s00?ie=UTF8&psc=1 (https://www.amazon.com/gp/product/B083CKZR5K/ref=ppx_yo_dt_b_asin_title_o02_s00?ie=UTF8&psc=1)

Amazon | 1 | MDR-60-24 | $19.99 | $19.99 | MEAN WELL MDR-60-24 DIN-Rail Power Supply 24V 2.5 Amp 60W

https://www.amazon.com/gp/product/B005T6OBFU/ref=ppx_yo_dt_b_asin_title_o01_s00?ie=UTF8&psc=1 (https://www.amazon.com/gp/product/B005T6OBFU/ref=ppx_yo_dt_b_asin_title_o01_s00?ie=UTF8&psc=1)
Amazon | 1 | MDR-60-5 | $21.47 | $21.47 | MEAN WELL MDR-60-5 AC to DC DIN-Rail Power Supply 5V 10 Amp 50W | https://www.amazon.com/gp/product/B005T6SAJI/ref=ppx_yo_dt_b_asin_title_o01_s01?ie=UTF8&psc=1 (https://www.amazon.com/gp/product/B005T6SAJI/ref=ppx_yo_dt_b_asin_title_o01_s01?ie=UTF8&psc=1)
Amazon | 2 | BE-032-3-fba | $12.99 | $25.98 | 2PCS 10mm to 10mm Aluminium Plum Flexible Shaft Coupling Diameter 20mm Length 25mm Connector Flexible Coupler for 3D Printer CNC Machine and Servo Stepped Motor（10x10mm） | https://www.amazon.com/gp/product/B07TF63R4C/ref=ppx_yo_dt_b_asin_title_o01_s01?ie=UTF8&psc=1 (https://www.amazon.com/gp/product/B07TF63R4C/ref=ppx_yo_dt_b_asin_title_o01_s01?ie=UTF8&psc=1)
Amazon | 1 | EAN# 0737123111343 | $35.89 | $35.89 | DIN Rail Terminal Block Kit #2 Red/Black Dinkle 20 DK4N 10 AWG Gauge 30A 600V Ground DK4N-PE Jumper DSS4N-10P End Covers End Brackets | https://www.amazon.com/gp/product/B07NVVBY98/ref=ppx_y
o_dt_b_asin_title_o09_s08?ie=UTF8&psc=1 (https://www.amazon.com/gp/product/B07NVVBY98/ref=ppx_yo_dt_b_asin_title_o09_s08?ie=UTF8&psc=1)
Amazon | 1 | AFB01F2P | $18.99 | $18.99 | Automation Systems Interconnect ASI AFB01F2P DIN Rail Mounted Midget Fuse Holder, 2 Pole, 10 x 38 mm, 13/32" Diameter x 1.5" Length, 18 to 8 AWG, 30 Amp, 600V | https://www.amazon.com/gp/product/B00W4XV1XQ/ref=ppx_yo_dt_b_asin_title_o09_s08?ie=UTF8&psc=1 (https://www.amazon.com/gp/product/B00W4XV1XQ/ref=ppx_yo_dt_b_asin_title_o09_s08?ie=UTF8&psc=1)
Amazon | 1 | GLD11-40 (EAN# 0791294549923) | $18.99 | $18.99 | Electrical Buddy Universal Switch 2 Position 3 Phase Panel Rotary Selector Changeover Switch GLD11 40A AC 690V 40A | https://www.amazon.com/gp/product/B07TJW9V1V/ref=ppx_y
o_dt_b_asin_title_o09_s08?ie=UTF8&psc=1 (https://www.amazon.com/gp/product/B07TJW9V1V/ref=ppx_yo_dt_b_asin_title_o09_s08?ie=UTF8&psc=1)
Amazon | 1 | Batige - USBHDMI | $10.99 | $10.99

BATIGE USB 3.0 & HDMI to HDMI + USB3.0 AUX Extension Dash Panel Waterproof Car Flush Mount Cable for Car Boat and Motorcycle - 3ft https://www.amazon.com/gp/product/B073HZ4STM/ref=ppx_yo_dt_b_asin_title_o09_s07?ie=UTF8&psc=1 (https://www.amazon.com/gp/product/B073HZ4STM/ref=ppx_yo_dt_b_asin_title_o09_s07?ie=UTF8&psc=1)
Amazon | 1 | ASIN# B07VYWW2HG | $24.99 | $24.99 | CNLINKO LP24 Aviation Connector M24 Male Plug with Female Socket Waterproof Metal Thread Panel Connector 4 Pins for AC DC Signal LED Lighting Equipment | https://www.amazon.com/gp/product/B07VYWW2HG/ref=ppx_yo_dt_b_asin_title_o09_s06?ie=UTF8&psc=1 (https://www.amazon.com/gp/product/B07VYWW2HG/ref=ppx_yo_dt_b_asin_title_o09_s06?ie=UTF8&psc=1)
Amazon | 1 | ASIN# B07GZBXGR7 | $7.99 | $7.99 | 5PCS GX16-6, 6Pins, 16mm, Panel Metal Mount Circular Metal Aviation Connector Adapter Male Female Plug Socket (5 Pcs Set) | https://www.amazon.com/gp/product/B07GZBXGR7/ref=ppx_yo_dt_b_asin_title_o09_s05?ie=UTF8&psc=1 (https://www.amazon.com/gp/product/B07GZBXGR7/ref=ppx_yo_dt_b_asin_title_o09_s05?ie=UTF8&psc=1)
Amazon | 1 | ASIN# B0753FF184 | $22.99 | $22.99 | 5PCS GX20-4, 4Pins, 20mm, Panel Metal Mount Circular Metal Aviation Connector Adapter Male Female Plug Socket (5 Pcs Set) | https://www.amazon.com/gp/product/B0753FF184/ref=ppx_yo_dt_b_asin_title_o09_s03?ie=UTF8&psc=1 (https://www.amazon.com/gp/product/B0753FF184/ref=ppx_yo_dt_b_asin_title_o09_s03?ie=UTF8&psc=1)
Amazon | 1 | ASIN# B08H8JM451 | $9.99 | $9.99 | RJ45 Shielded Industrial Dual Panel Mount Female to Female Coupler Panel Mount Waterproof Connector Combo with Cap Network Connectors Cat5/5e/6 8P8C Connector Waterproof Cover (2 Pack, Black) | https://www.amazon.com/gp/product/B08H8JM451/ref=ppx_yo_dt_b_asin_title_o09_s03?ie=UTF8&psc=1 (https://www.amazon.com/gp/product/B08H8JM451/ref=ppx_yo_dt_b_asin_title_o09_s03?ie=UTF8&psc=1)
Amazon | 1 | ASIN# B078S17FZ5 | $8.00 | $8.00 | 10Pcs Black US 3 Pins Power Socket Plug Panel Screw Mount Type Female Connectors Adapter | https://www.amazon.com/gp/product/B078S17FZ5/ref=ppx_yo_dt_b_asin_title_o09_s03?ie=UTF8&psc=1 (https://www.amazon.com/gp/product/B078S17FZ5/ref=ppx_yo_dt_b_asin_title_o09_s03?ie=UTF8&psc=1)
Amazon | 1 | ASIN# B088FX3S8J | $5.81 | $5.81 | USB to RS485 Converter Adapter CH340T Chip 64-bit Suitable for Windows 7 8 10 (Pack of 2) | https://www.amazon.com/gp/product/B088FX3S8J/ref=ppx_yo_dt_b_asin_title_o09_s01?ie=UTF8&psc=1 (https://www.amazon.com/gp/product/B088FX3S8J/ref=ppx_yo_dt_b_asin_title_o09_s01?ie=UTF8&psc=1)
Amazon | 1 | E5-9JOT-1VXO | $12.99 | $12.99 | TWTADE/Red Mushroom Cap 1NO 1NC DPST Emergency Stop Push Button Switch AC 660V 10A (Quality Assurance for 3 Years) YW1B-V4E11R | https://www.amazon.com/gp/product/B07C2NJN94/ref=ppx_yo_dt_b_asin_title_o09_s01?ie=UTF8&psc=1 (https://www.amazon.com/gp/product/B07C2NJN94/ref=ppx_yo_dt_b_asin_title_o09_s01?ie=UTF8&psc=1)

*** Note: There are multiple tabs to this BOM. This page is what I expressly bought when I built it and the prices I paid. The next tab is a solidworks geberated BOM with every part in the assembly called out by assembly QTY.

Amazon | 1 | ASIN# B06XRT2YFV | $15.99 | $15.99

5PCS GX12-3, 3Pins, 12mm, Panel Metal Mount Circular Metal Aviation Connector Adapter Male Female Plug Socket (5 Pcs Set) https://www.amazon.com/gp/product/B06XRT2YFV/ref=ppx_yo_dt_b_asin_title_o09_s00?ie=UTF8&psc=1 (https://www.amazon.com/gp/product/B06XRT2YFV/ref=ppx_yo_dt_b_asin_title_o09_s00?ie=UTF8&psc=1)
Amazon | 1 | ASIN# B07TT4HH5L | $18.99 | $18.99 | 1238 48V Fan, 120mm x 38mm Dual Ball Bearings DC Brushless Cooling Fan | https://www.amazon.com/gp/product/B07TT4HH5L/ref=ppx_yo_dt_b_asin_title_o08_s01?ie=UTF8&psc=1 (https://www.amazon.com/gp/product/B07TT4HH5L/ref=ppx_yo_dt_b_asin_title_o08_s01?ie=UTF8&psc=1)
Amazon | 1 | ASIN# B075Q55ZNN | $9.99 | $9.99 | 120mm Fan Filter 2 Pack IP40 Dustproof Blower Guard ABS Computer Ventilator Grill 12cm Fan Mesh Cover Tool-Free Fan Strainer Compatible for 120x120 Case Fan USB Cooling Fan | https://www.amazon.com/gp/product/B075Q55ZNN/ref=ppx_y

o_dt_b_asin_title_o08_s00?ie=UTF8&psc=1 (https://www.amazon.com/gp/product/B075Q55ZNN/ref=ppx_yo_dt_b_asin_title_o08_s00?ie=UTF8&psc=1)
Amazon | 3 | ASIN# B07HBT3442 | $16.99 | $50.97 | R55 1M Length Plastic Closed can Open Cable Drag Chain Wire Carrier (25x57mm) | https://www.amazon.com/gp/product/B07HBT3442/ref=ppx_yo_dt_b_asin_title_o07_s01?ie=UTF8&psc=1 (https://www.amazon.com/gp/product/B07HBT3442/ref=ppx_yo_dt_b_asin_title_o07_s01?ie=UTF8&psc=1)
Amazon | 1 | ASIN# B077Z1W2HJ | $36.00 | $36.00 | Wokesi 14Pcs,ER20 1mm 2mm 3mm 4mm 5mm 6mm 7mm 8mm 9mm 10mm 11mm 12mm 13mm 1/8 Clamping Diameter,Spring Collet Chuck Set For CNC Lathe Machine Mill Tool(COLLET DIA:1mm-13mm T.I.R:8um,ER20) | https://www.amazon.com/gp/product/B077Z1W2HJ/ref=ppx_y

o_dt_b_asin_title_o06_s01?ie=UTF8&psc=1 (https://www.amazon.com/gp/product/B077Z1W2HJ/ref=ppx_yo_dt_b_asin_title_o06_s01?ie=UTF8&psc=1)
Amazon | 1 | EAN# 0753922958088 | $28.49 | $28.49 | CNC Spoilboard Surfacing Router Bits, 1/2 inch Shank 2 inch Cutting Diameter, Slab Flattening Router Bit Planing Bit Wood Milling Cutter Planer Woodworking Tool by NITOMAK (Carbide) | https://www.amazon.com/gp/product/B07WQG85HV/ref=ppx_yo_dt_b_asin_title_o05_s00?ie=UTF8&psc=1 (https://www.amazon.com/gp/product/B07WQG85HV/ref=ppx_yo_dt_b_asin_title_o05_s00?ie=UTF8&psc=1)
Amazon | 2 | ASIN# B07V4PR84Y | $10.99 | $21.98 | 3Pcs TL-W5MC1 5mm 3 Wire Inductive Proximity Sensor Detection Switch NPN DC 6-36V | https://www.amazon.com/gp/product/B07V4PR84Y/ref=ppx_yo_dt_b_asin_title_o03_s00?ie=UTF8&psc=1 (https://www.amazon.com/gp/product/B07V4PR84Y/ref=ppx_yo_dt_b_asin_title_o03_s00?ie=UTF8&psc=1)
Amazon | 1 | ASIN# B08514H2BJ | $27.00 | $27.00 | 5pcs ER20 Nut for Clamping collets, Balanced to G2.5/25000rpm-NUT-ER20-G25-New | https://www.amazon.com/gp/product/B08514H2BJ/ref=ppx_yo_dt_b_asin_title_o02_s00?ie=UTF8&psc=1 (https://www.amazon.com/gp/product/B08514H2BJ/ref=ppx_yo_dt_b_asin_title_o02_s00?ie=UTF8&psc=1)
Amazon | 1 | YC-ENC-FE-S YC-20X16X10-UL-FE | $196.00 | $196.00 | Yuco YC-20X16X10-UL-FE Fully Enclosed (no gland plate) IP66 Enclosure, UL Certified, Nema 4, 16 Gauge, Single Door Hinge Cover, Wall-Mount, Backplate (20 x 16 x 10) | https://www.amazon.com/gp/product/B074XGTHCK/ref=ppx_yo_dt_b_asin_title_o01_s00?ie=UTF8&psc=1 (https://www.amazon.com/gp/product/B074XGTHCK/ref=ppx_yo_dt_b_asin_title_o01_s00?ie=UTF8&psc=1)
Amazon | 1 | ASIN# B07RXK96GV | $4.99 | $4.99 | 10 Pcs FC-26P 2x13 Pin 2.54mm Dual Rows Female Header IDC Cable Connector | https://www.amazon.com/gp/product/B07RXK96GV/ref=ppx_yo_dt_b_asin_title_o00_s00?ie=UTF8&psc=1 (https://www.amazon.com/gp/product/B07RXK96GV/ref=ppx_yo_dt_b_asin_title_o00_s00?ie=UTF8&psc=1)
Amazon | 1 | ASIN# B07P9GM8H1 | $9.99 | $9.99 | 10Ft/3M IDC 26P 1.27mm Rainbow Color Flat Ribbon Wire | https://www.amazon.com/gp/product/B07P9GM8H1/ref=ppx_yo_dt_b_asin_title_o09_s00?ie=UTF8&psc=1 (https://www.amazon.com/gp/product/B07P9GM8H1/ref=ppx_yo_dt_b_asin_title_o09_s00?ie=UTF8&psc=1)
Amazon | 1 | EAN# 0713072774679 | $10.59 | $10.59 | 10 Pcs 6000-2RS Double Rubber Seal Bearings 10x26x8mm, Pre-Lubricated and Stable Performance and Cost Effective, Deep Groove Ball Bearings. | https://www.amazon.com/gp/product/B072F6J3GN/ref=ppx_yo_dt_b_asin_title_o08_s00?ie=UTF8&psc=1 (https://www.amazon.com/gp/product/B072F6J3GN/ref=ppx_yo_dt_b_asin_title_o08_s00?ie=UTF8&psc=1)
Amazon | 7 | ASIN# B07L11S1Q4 | $9.89 | $69.23 | Slide in T-Nut, M5 Threaded for 4040 Series Aluminum Extrusions Profile, Pack of 12 | https://www.amazon.com/gp/product/B07L11S1Q4/ref=ppx_yo_dt_b_asin_title_o07_s01?ie=UTF8&psc=1 (https://www.amazon.com/gp/product/B07L11S1Q4/ref=ppx_yo_dt_b_asin_title_o07_s01?ie=UTF8&psc=1)
Amazon | 1 | ASIN# B01LZA04NX | $41.49 | $41.49 | R55 25mm x 38mm Plastic Cable Wire Carrier Drag Chain 1M Black for CNC | https://www.amazon.com/uxcell-Plastic-Cable-Carrier-Chain/dp/B01LZA04NX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 (https://www.amazon.com/uxcell-Plastic-Cable-Carrier-Chain/dp/B01LZA04NX?s=industrial)
Amazon | 1 | EAN# 0737123110988 | $29.99 | $29.99 | Dinkle DIN Rail Block Kit #2 DIN Rail Terminal Block Kit Dinkle 20 DK4N 10 AWG Gauge Ground DK4N-PE Jumper DSS4N-10P End Covers End Brackets,30 Amp, 600V | https://www.amazon.com/gp/product/B01IDL6OW0/ref=ppx_yo_dt_b_asin_title_o05_s00?ie=UTF8&psc=1 (https://www.amazon.com/gp/product/B01IDL6OW0/ref=ppx_yo_dt_b_asin_title_o05_s00?ie=UTF8&psc=1)
Amazon | 1 | EAN# 0737123111329 | $28.99 | $28.99 | Dinkle UL Every Color DIN Rail Terminal Block Kit 20 DK2.5N 12 AWG Gauge 20A 600V Ground DK4N-PE Jumper DSS2.5N-10P End Covers End Brackets | https://www.amazon.com/gp/product/B07NVV28D9/ref=ppx_y
o_dt_b_asin_title_o05_s00?ie=UTF8&psc=1 (https://www.amazon.com/gp/product/B07NVV28D9/ref=ppx_yo_dt_b_asin_title_o05_s00?ie=UTF8&psc=1)
Amazon | 1 | 43235-27956 | $11.50 | $11.50 | 2 Ports Dual USB 3.0 Male to USB 3.0 Female AUX Flush Mount Car Mount Extension Cable for Car Truck Boat Motorcycle Dashboard Panel -(3 Feet) | | https://www.amazon.com/gp/product/B01MY1WDIU/ref=ppx_yo_dt_b_asin_title_o04_s00?ie=UTF8&psc=1 (https://www.amazon.com/gp/product/B01MY1WDIU/ref=ppx_yo_dt_b_asin_title_o04_s00?ie=UTF8&psc=1)
Amazon | 1 | 2KTK20 | $10.99 | $10.99 | KTK-20 Fast Acting Limitron Fuse 600 VAC 20A (2 Pack) QSU | | https://www.amazon.com/gp/product/B07VH8RDLV/ref=ppx_yo_dt_b_asin_title_o01_s01?ie=UTF8&psc=1 (https://www.amazon.com/gp/product/B07VH8RDLV/ref=ppx_yo_dt_b_asin_title_o01_s01?ie=UTF8&psc=1)
Amazon | 1 | EAN# 0712994005847 | $13.99 | $13.99 | Rocaris 5 Pcs M3 M4 M5 M6 M8 Titanium Coated HSS Spiral Flute Metric Taps Set | | https://www.amazon.com/gp/product/B01JSAFB92/ref=ppx_yo_dt_b_asin_title_o00_s01?ie=UTF8&psc=1 (https://www.amazon.com/gp/product/B01JSAFB92/ref=ppx_yo_dt_b_asin_title_o00_s01?ie=UTF8&psc=1)
Amazon | 1 | A03-DDK01-S-KH | $33.99 | $33.99 | Kehuashina CNC Z-Axis Router Mill Touch Plate Mach3 Tool Setting Probe Milling Tools Silver | | https://www.amazon.com/gp/product/B07FLQRKPN/ref=ppx_yo_dt_b_asin_title_o05_s00?ie=UTF8&psc=1 (https://www.amazon.com/gp/product/B07FLQRKPN/ref=ppx_yo_dt_b_asin_title_o05_s00?ie=UTF8&psc=1)
Amazon | 1 | ASIN# B08FDGJMVF | $399.90 | $399.90 | Minisforum - UM300 Mini PC AMD Ryzen 3 3300U Windows 10 Pro Mini PC Desktop Computer, Radeon Vega 6 Graphics,8GB DDR4 256GB SSD,HDMI2.0/DP/USB-C Triple 4K@60Hz Output,with1000M LAN Intel WIFI6 AX200 BT5.1 | | https://www.amazon.com/gp/product/B08FDGJMVF/ref=ppx_yo_dt_b_asin_title_o01_s00?ie=UTF8&psc=1 (https://www.amazon.com/gp/product/B08FDGJMVF/ref=ppx_yo_dt_b_asin_title_o01_s00?ie=UTF8&psc=1)
Amazon | 1 | ASIN# B01HOM9IZ4 | $26.99 | $26.99 | TEAMGROUP Elite 8GB Single DDR4 2400MHz PC4-19200 CL16 Unbuffered Non-ECC 1.2V SODIMM 260-Pin Laptop Notebook PC Computer Memory Module Ram Upgrade -TED48G2400C16-S01 - (1x 8GB) Single | | https://www.amazon.com/gp/product/B01HOM9IZ4/ref=ppx_yo_dt_b_asin_title_o01_s00?ie=UTF8&psc=1 (https://www.amazon.com/gp/product/B01HOM9IZ4/ref=ppx_yo_dt_b_asin_title_o01_s00?ie=UTF8&psc=1)
Amazon | 1 | ASIN# B07LD1HPYC | $13.99 | $13.99 | Beduan 8mm x 5mm Clear Pneumatic Tubing Pipe PU Polyurethane Air Compressor Tubing Hose Pipe Line Fluid Transfer 39.4ft 12 Meter | | https://www.amazon.com/gp/product/B07LD1HPYC/ref=ppx_yo_dt_b_asin_title_o00_s01?ie=UTF8&psc=1 (https://www.amazon.com/gp/product/B07LD1HPYC/ref=ppx_yo_dt_b_asin_title_o00_s01?ie=UTF8&psc=1)
Amazon | 1 | ASIN# B07D9JKT91 | $14.99 | $14.99 | fosa G1/4 Threaded Computer Water Cooling System Flow Meter Indicator Acrylic Replacement for PC Computer … | Need to wire pump at 12V (100% duty cycle) for this to function | https://www.amazon.com/gp/product/B07D9JKT91/ref=ppx_yo_dt_b_asin_title_o00_s01?ie=UTF8&psc=1 (https://www.amazon.com/gp/product/B07D9JKT91/ref=ppx_yo_dt_b_asin_title_o00_s01?ie=UTF8&psc=1)
Amazon | 1 | TBJ4812B60Z | $16.98 | $16.98 | DC Voltage Regulator Buck Converter DC 48V Step Down to 12V 5A 60W Reducer Power Converter Waterproof Module Transformer for Golf Cart Club Car | Mounted in bottom of control cabinet | https://www.amazon.com/gp/product/B07V8J6BJQ/ref=ppx_yo_dt_b_asin_title_o00_s01?ie=UTF8&psc=1 (https://www.amazon.com/gp/product/B07V8J6BJQ/ref=ppx_yo_dt_b_asin_title_o00_s01?ie=UTF8&psc=1)
Amazon | 1 | ASIN# B07QYFKCJB | $11.79 | $11.79 | fosa Pointer Display Thermometer with Waterproof Probe, PC G1/4 Thread Water Cooling System Temperature Meter for Computer Laptop | This can be wired at 12V or 5V | https://www.amazon.com/gp/product/B07QYFKCJB/ref=ppx_yo_dt_b_asin_title_o00_s01?ie=UTF8&psc=1 (https://www.amazon.com/gp/product/B07QYFKCJB/ref=ppx_yo_dt_b_asin_title_o00_s01?ie=UTF8&psc=1)

Amazon | 1 | ASIN# B07GS3JPW1 | $11.39 | $11.39 | Aramox 6 PCS Barb-Fitting, PC Water Cooling Two-Touch Fitting G1/4 Thread Barb Connector for Tube (6mm) | | https://www.amazon.com/gp/product/B07GS3JPW1/ref=ppx_od_dt_b_asin_title_s00?ie=UTF8&psc=1 (https://www.amazon.com/gp/product/B07GS3JPW1/ref=ppx_od_dt_b_asin_title_s00?ie=UTF8&psc=1)
Amazon | 1 | ASIN# B07TZJH7VD | $71.39 | $71.39 | Bewinner 800L/H Mini Water Cooling Pump 0.7A 7V 12cm/ 4.72in, 17cm/ 6.69in / Note I filled my loop with RV Antifreeze (pink stuff). Works well and keeps the loop from freezing in my garage in the winter months. | AKA Freezemod FS6PD-17 Pump and Resevoive combo (https://freezemod.com/product-category/reservoir-pump-kit/) | https://www.amazon.com/gp/product/B07TZJH7VD/ref=ppx_o

d_dt_b_asin_title_s01?ie=UTF8&psc=1 (https://www.amazon.com/gp/product/B07TZJH7VD/ref=ppx_od_dt_b_asin_title_s01?ie=UTF8&psc=1)
Amazon | 2 | NF-P12 redux-1700 PWM | $13.90 | $27.80 | Noctua NF-P12 redux-1700 PWM, High Performance Cooling Fan, 4-Pin, 1700 RPM (120mm, Grey) | | https://www.amazon.com/gp/product/B07CG2PGY6/ref=ppx_od_dt_b_asin_title_s01?ie=UTF8&psc=1 (https://www.amazon.com/gp/product/B07CG2PGY6/ref=ppx_od_dt_b_asin_title_s01?ie=UTF8&psc=1)
Amazon | 1 | ASIN# B07XCNLKGY | $16.99 | $16.99 | SDTC Tech 4-Pack G1/4" Male to Female Extender Connector 90° Rotary Elbow Enhance Multi-Link Adapter Fitting for PC Water Cooling System, Black | Notes: ModMyMods is much cheaper on watercooling parts | https://www.amazon.com/gp/product/B07XCNLKGY/ref=ppx_od_dt_b_asin_title_s01?ie=UTF8&psc=1 (https://www.amazon.com/gp/product/B07XCNLKGY/ref=ppx_od_dt_b_asin_title_s01?ie=UTF8&psc=1)
Amazon | 1 | 5060175582614 | $65.48 | $65.48 | XSPC EX240 Radiator, 120mm x 2, Dual Fan, Multiport, Black | Notes: ModMyMods is much cheaper on watercooling parts | https://www.amazon.com/gp/product/B008BWR17E/ref=ppx_od_dt_b_asin_title_s01?ie=UTF8&psc=1 (https://www.amazon.com/gp/product/B008BWR17E/ref=ppx_od_dt_b_asin_title_s01?ie=UTF8&psc=1)
Amazon | 1 | ASIN# B08NX29CB3 | $9.99 | $9.99 | DGZZI Black G1/4 Inch Rotary Male to Male Extender Fitting | Notes: ModMyMods is much cheaper on watercooling parts | https://www.amazon.com/dp/B08NX29CB3/ref=cm_sw_r_cp_apa_fabc_hG98FbNE7CREV (https://www.amazon.com/dp/B08NX29CB3/ref=cm_sw_r_cp_apa_fabc_hG98FbNE7CREV)
Amazon | 1 | ASIN# B07XDLDYYR | $13.99 | $13.99 | SDTC Tech 6 Pack G1/4" Plug Fitting with O-Ring for PC Water Cooling Systems, Black | Notes: ModMyMods is much cheaper on watercooling parts | https://www.amazon.com/dp/B07XDLDYYR/ref=cm_sw_r_cp_apa_fabc_UA98FbJZPRZC4 (https://www.amazon.com/dp/B07XDLDYYR/ref=cm_sw_r_cp_apa_fabc_UA98FbJZPRZC4)
Amazon | 1 | ASIN# B07X7WKGSK | $16.99 | $16.99 | SDTC Tech G1/4" Ball Valve Water Shutoff Valve Fitting for PC Water Cooling Systems | Notes: ModMyMods is much cheaper on watercooling parts | https://www.amazon.com/dp/B07X7WKGSK/ref=cm_sw_r_cp_apa_fabc_2D98Fb21W0TQC (https://www.amazon.com/dp/B07X7WKGSK/ref=cm_sw_r_cp_apa_fabc_2D98Fb21W0TQC)
Amazon | 1 | TX4T-A01 | $15.00 | $15.00 | G1/4" 4-Way Ball Fitting, Rotary, Black | Notes: ModMyMods is much cheaper on watercooling parts | https://www.amazon.com/dp/B01M4KGFQH/ref=cm_sw_r_cp_apa_fabc_RP98FbYFMKPMR (https://www.amazon.com/dp/B01M4KGFQH/ref=cm_sw_r_cp_apa_fabc_RP98FbYFMKPMR)
Amazon | 1 | CP621200 | $30.99 | $30.99 | Ferrule Crimping Tool Kit, Preciva AWG23-7 Self-adjustable Ratchet Wire Crimping Tool Kit Crimper Plier Set with 1200PCS Wire Terminals Crimping Connectors Wire End Ferrules | | https://www.amazon.com/gp/product/B073TZ5BBG/ref=ppx_y
o_dt_b_search_asin_title?ie=UTF8&psc=1 (https://www.amazon.com/gp/product/B073TZ5BBG/ref=ppx_yo_dt_b_search_asin_title?ie=UTF8&psc=1)
StepperOnline | 2 | CE3-M3-18 | $15.15 | $30.30

2.7m(106") AWG18 Motor and Encoder Extension Cable Kit for Nema 34 Closed Loop Stepper Motors

https://www.omc-stepperonline.com/cable-kit-2-7-m-106-longmotor-extension-cable-and-2-7-m-106-long-encoderextension-cable-for-nema-34-closed-loop-stepper-motors-just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 (https://www.omc-stepperonline.com/cable-kit-2-7-m-106-long-motor-extension-cable-and-2-7-m-106-long-encoder-extension-cable-for-nema-34-closed-loop-stepper-mo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)

StepperOnline | 2 | CE5-M5-18 | $22.89 | $45.78

4.7m(185") AWG18 Motor and Encoder Extension Cable Kit for Nema 34 Closed Loop Stepper Motors

https://www.omc-stepperonline.com/cable-kit-4-7-m-185-longmotor-extension-cable-and-4-7-m-185-long-encoderextension-cable-for-nema-34-closed-loop-stepper-motors-just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 (https://www.omc-stepperonline.com/cable-kit-4-7-m-185-long-motor-extension-cable-and-4-7-m-185-long-encoder-extension-cable-for-nema-34-closed-loop-stepper-mo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)

StepperOnline | 4 | 1-CL57Y-24HE34 | $91.15 | $364.60

YE Series 1 Axis Closed Loop Stepper CNC Kit 3.0 Nm(424.92oz.in) Nema 24 Motor & Driver

https://www.omc-stepperonline.com/ye-series-1-axis-closedloop-stepper-cnc-kit-3-0-nm-424-92oz-in-nema-24-motor-anddriver.html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 (https://www.omc-stepperonline.com/ye-series-1-axis-closed-loop-stepper-cnc-kit-3-0-nm-424-92oz-in-nema-24-motor-and-driver.html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)
CNC4PC | 1 | AXBB_B-AXBB-UCCNC_B | $253.00 | $253.00 | AXBB-E Ethernet Motion Controller and Breakout Board Combined Motion Controller Unit (QTY:1 AXBB-E ethernet motion controller and breakout board combined controller / QTY:1 UCCNC License File Bundle) | https://www.cnc4pc.com/axbb-e-ethernet-motion-controller-and-breakout-board-combined-controller-b.html (https://www.cnc4pc.com/axbb-e-ethernet-motion-controller-and-breakout-board-combined-controller-b.html)
CNC4PC | 1 | UCSB | $64.00 | $64.00 | UCSB single port breakout board | https://www.cnc4pc.com/ucsb-single-port-breakout-board.html
CNC4PC | 1 | S-1000-48 | $119.00 | $119.00 | 48V/20A Switching CNC Power supply | https://www.cnc4pc.com/48v-20a-switching-cnc-power-supply.html (https://www.cnc4pc.com/48v-20a-switching-cnc-power-supply.html)
AliExpress | 1 | HY02D223B | $217.00 | $217.00 | HUANYANG high quality 4 bearings 2.2KW 220V water cooled spindle motor for engraving machine CNC router ER20 24000rpm | https://www.aliexpress.com/item/32801003817.html?spm=a2 g0s.9042311.0.0.14544c4dWvmmZd (https://www.aliexpress.com/item/32801003817.html?spm=a2g0s.9042311.0.0.14544c4dWvmmZd)
AliExpress | 1 | GT-2R2G-2 | $135.00 | $135.00 | 2.2KW 220V AC drive vector control inverter frequency inverter VFD HUANYANG (HYRIA) variable | https://www.aliexpress.com/item/32754134517.html?spm=a2 g0s.9042311.0.0.14544c4dWvmmZd (https://www.aliexpress.com/item/32754134517.html?spm=a2g0s.9042311.0.0.14544c4dWvmmZd)
AliExpress | 2 | YY-M-15 80mm | $10.14 | $20.28 | Aluminum Router/Spindle Mount Diameter 80mm | https://www.aliexpress.com/item/32816643732.html?spm=a2 g0s.9042311.0.0.14544c4dWvmmZd (https://www.aliexpress.com/item/32816643732.html?spm=a2g0s.9042311.0.0.14544c4dWvmmZd)

Automation Direct | 25 | SEOOW-16-4BK-1 | $0.59 | $14.75 | Southwire flexible portable cord, Type SEOOW, 600V, 4 conductors (includes ground), 16 AWG, TPE conductor insulation material, black, white, red and green, TPE jacket, black, cut to length. | https://www.automationdirect.com/adc/shopping/catalog/cables/bulk_multi-conductor_cable/flexible_portable_cord_(sjoow,_soow,_sjeoow,_seoow,_type_w)/insulation_type_-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 (https://www.automationdirect.com/adc/shopping/catalog/cables/bulk_multi-conductor_cable/flexible_portable_cord_(sjoow,_soow,_sjeoow,_seoow,_type_w)/insulation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)
Automation Direct | 25 | SEOOW-10-4BK-1 | $1.67 | $41.75 | Southwire flexible portable cord, Type SEOOW, 600V, 4 conductors (includes ground), 10 AWG, TPE conductor insulation material, black, white, red and green, TPE jacket, black, cut to length. | https://www.automationdirect.com/adc/shopping/catalog/cables/bulk_multi-conductor_cable/flexible_portable_cord_(sjoow,_soow,_sjeoow,_seoow,_type_w)/insulation_type_-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 (https://www.automationdirect.com/adc/shopping/catalog/cables/bulk_multi-conductor_cable/flexible_portable_cord_(sjoow,_soow,_sjeoow,_seoow,_type_w)/insulation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)
Automation Direct | 1 | AD-SSR210-22-DCZ | $42.50 | $42.50 | Solid state relay, 35mm DIN rail mount, finger-safe, 4-32 VDC input voltage, SPST, N.O. SCR, 10A contact rating, 24-280 VAC load voltage, zero cross, screw terminal(s), LED indicator(s). | https://www.automationdirect.com/adc/shopping/catalog/relays_-z-_timers/solid_state_relays/din_mount_relays_(ad-ssr8_-z-_ad-ssr2_-z-_ad-ssr6_-z-_ad-hssr8_series)/gen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,_(ad-ssr8_-z-_ad-

ssr2_-z-_ad-ssr6_series)/ad-ssr210-22-dcz (https://www.automationdirect.com/adc/shopping/catalog/relays_-z-_timers/solid_state_relays/din_mount_relays_(ad-ssr8_-z-_ad-ssr2_-z-_ad-ssr6_-z-_ad-hssr8_seri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)

Automation Direct | 1 | AD-SSR630-22-DCZ | $58.00 | $58.00

Solid state relay, 35mm DIN rail mount, finger-safe, 4-32 VDC input voltage, SPST, N.O. SCR, 30A contact rating, 48-660 VAC load voltage, zero cross, screw terminal(s), LED indicator(s).

https://www.automationdirect.com/adc/shopping/catalog/relays_-z-_timers/solid_state_relays/din_mount_relays_(ad-ssr8_-z-_ad-ssr2_-z-_ad-ssr6_-z-_adhssr8_series)/gene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,_(ad-ssr8_-z-_ad-ssr2_-z-_ad-ssr6_series)/ad-ssr630-22-dcz (https://www.automationdirect.com/adc/shopping/catalog/relays_-z-_timers/solid_state_relays/din_mount_relays_(ad-ssr8_-z-_ad-ssr2_-z-_ad-ssr6_-z-_ad-hssr8_seri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)
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

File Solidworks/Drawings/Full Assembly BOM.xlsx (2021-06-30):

LienCNC V2 | See Print
ITEM NO. | QTY. | PART NUMBER | DESCRIPTION
1 | 1 | CNC Base and Electronics | Assembly
1.1 | 1 | Workbench | Wood
1.1.1 | 1 | 2x4 Frame | Lumber Frame
1.1.1.1 | 654 in | 2x4 (Pine) | 2x4 Lumber (1.5" x 3.5")
1.1.2 | 1 | Workbench Lower Shelf | 3/4" Plywood or MDF
1.1.3 | 1 | Workbench Top | 3/4" Plywood or MDF
1.1.4 | 2 | 2406T34 | Ridged Caster
1.1.5 | 2 | 2406T29 | Swivel Caster
1.1.6 | 1 | Shelf Back Panel | 3/4" Plywood or MDF
1.1.7 | 16 | 92351A544 | 1/4" x 1-1/4"L Lag
1.2 | 1 | LienCNC_Base | CNC Base Frame
1.2.1 | 1 | 8020_Base_Frame | 8020 Aluminum Frame Components
1.2.1.1 | 2 | 40-4012 | 80/20 40-4012 PROFILE
1.2.1.2 | 4 | 40-4080 | 80/20 40-4080 PROFILE
1.2.2 | 1 | Spoilboard (Bottom) | 3/4" MDF Bottom Spoilboard
1.2.3 | 1 | Spoilboard (Top) | 3/4" MDF Top Spoilboard
1.2.4 | 36 | 98689A116 | 8mm SST Washer
1.2.5 | 16 | 91292A208 | SCS M8 x 1.25 x 45mm Long PT (SST)
1.2.6 | 20 | 8mm SCS SST x 25mm - DIN 912, ISO 4762 | Stainless Steel M8 Socket Head Cap Screw
1.2.7 | 4 | 40-2849 (8020 Foot) | 8020 Rubber Foot
1.2.8 | 8 | 40-1984 | M8 Tnut for 40 series Tslot
1.2.9 | 16 | 5mm SCS SST x 12mm | M5 SCS
1.2.10 | 16 | 98689A114 | 5mm SST Washer
1.2.11 | 16 | M5_Tnut_40Series-Profile | M5 Tnut for 40 series Tslot
1.2.12 | 1 | Y_Axis_Endplate | Front Right Y Axis Endplate
1.2.13 | 2 | Nema24_Yaxis_Endplate | Fabricated Aluminum Plate (Front Right Y Axis Endplate)
1.2.14 | 2 | Backsplash | 1/8" Aluminum Dust Backsplash
1.2.15 | 2 | Side Profiles | Angle Aluminum Side Dust Profiles
1.2.15.1 | 2 | 2x1.5x0.125in x 1000mm Long - Aluminum L Angle | L2x1.5x0.125 Aluminum L Angle
1.2.16 | 1 | MirrorY_Axis_Endplate | Fabricated Aluminum Plate (Mirror)
1.3 | 1 | CNC Control Panel | Electrical CNC Controls
1.3.1 | 1 | YuCo YC-20X16X10-UL | 16x20x10 Yuco Electronics Enclosure
1.3.1.1 | 2 | 87929507
1.3.1.1.1 | 1 | 87929767
1.3.1.1.2 | 1 | 87929769_Installed on Pin
1.3.1.2 | 1 | 87934540
1.3.1.2.1 | 1 | 99401225
1.3.1.2.2 | 4 | 23271001_After Weld
1.3.1.2.3 | 1 | 87934343
1.3.1.3 | 2 | 89076399
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

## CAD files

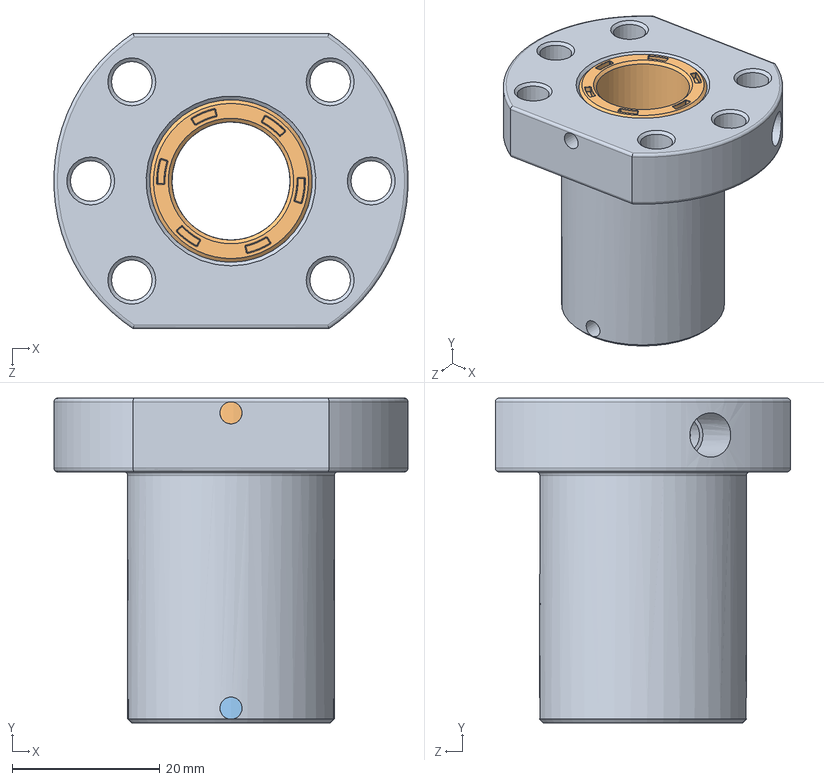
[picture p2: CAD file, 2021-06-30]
Solidworks/Hardware/SFU1605-1610.SLDASM
48.0 x 44.0 x 40.0 mm
SFU1605-1610-1
SFU1605-1610-3
SFU1605-1610-2

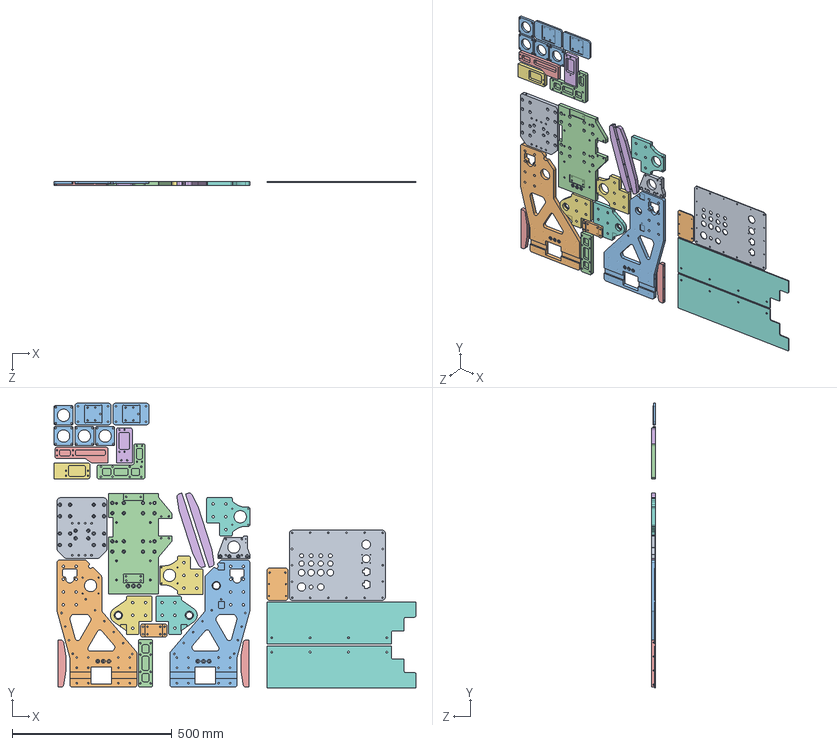
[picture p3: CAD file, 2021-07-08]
Solidworks/Machined Aluminum Parts/Machined Parts Nested.SLDASM
1132.8 x 891.0 x 12.7 mm
Z_Axis_Plate
Gantry_Riser
MirrorGantry_Riser
X_Axis_Plate
Gantry Rib2 x 2
Gantry Rib1 x 2
MirrorY_Axis_Endplate x 2
Y_Axis_Endplate x 2
Z_Axis_Motor_Plate
X-Axis_Ballscrew_Connection_Plate
Nema24_Spacer_Plate x 4
Z_Axis_Spacer x 2
Drag Chain Mount (Z Axis)
Drag Chain Mount (X Axis)
Drag Chain Mount (Y Axis)
Backsplash x 2
Controller Gland Plate
Freezemod PU-FS6M Mounting Bracket
Y-Axis_Ballscrew_Connection_Plate x 2

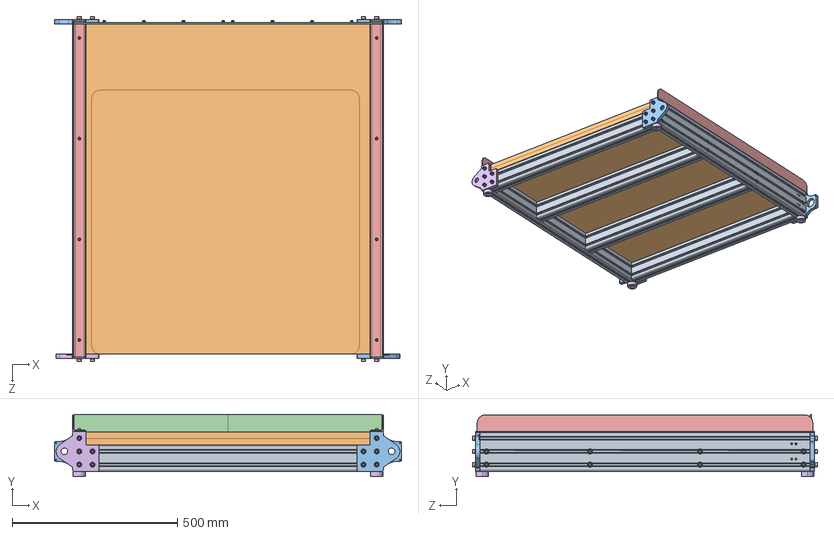
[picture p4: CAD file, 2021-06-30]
Solidworks/Sub Assemblies/LienCNC_Base.SLDASM
1050.0 x 187.7 x 1045.0 mm
8020_Base_Frame
Spoilboard x 2
8mm_Washer_SST x 36
91292A208_TYPE 18-8 SS SOCKET HEAD CAP SCREW x 16
8mm_SCS_SST x 20
40_2849 (8020 Foot) x 4
5mm_SCS_SST x 16
5mm_Washer_SST x 16
M5_Tnut_40Series-Profile x 16
Y_Axis_Endplate x 3
Backsplash x 2
Side Profiles x 2
MirrorY_Axis_Endplate

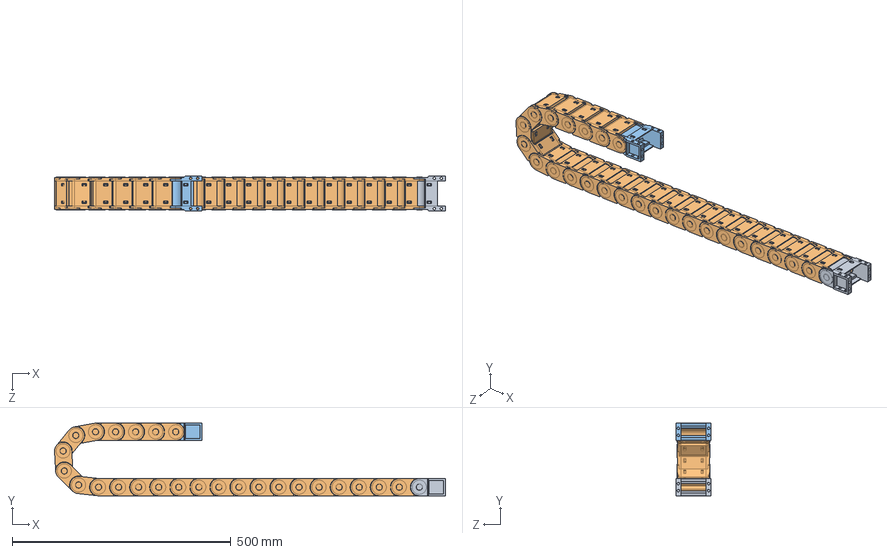
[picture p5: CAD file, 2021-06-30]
Solidworks/Sub Assemblies/H25 (25x57mm Drag Chain).SLDASM
893.2 x 165.9 x 78.9 mm
H25-EndLink1 (25x57_ID_Drag_Chain)
H25-CenterLink (25x57_ID_Drag_Chain) x 25
H25-EndLink2 (25x57_ID_Drag_Chain)

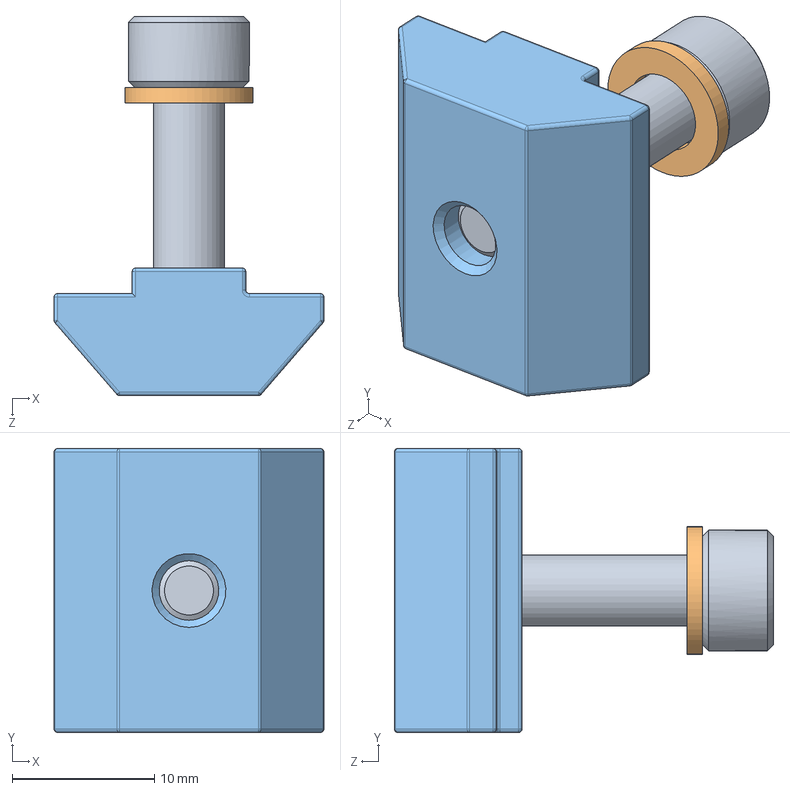
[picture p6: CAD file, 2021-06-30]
Solidworks/Hardware/M5_Rail_Mounting-Tnut_ASMB.SLDASM
19.0 x 20.0 x 26.7 mm
5mm_SCS_SST
98689A114_GENERAL PURPOSE 18-8 STAINLESS STEEL WASHER
M5_Tnut_40Series-Profile

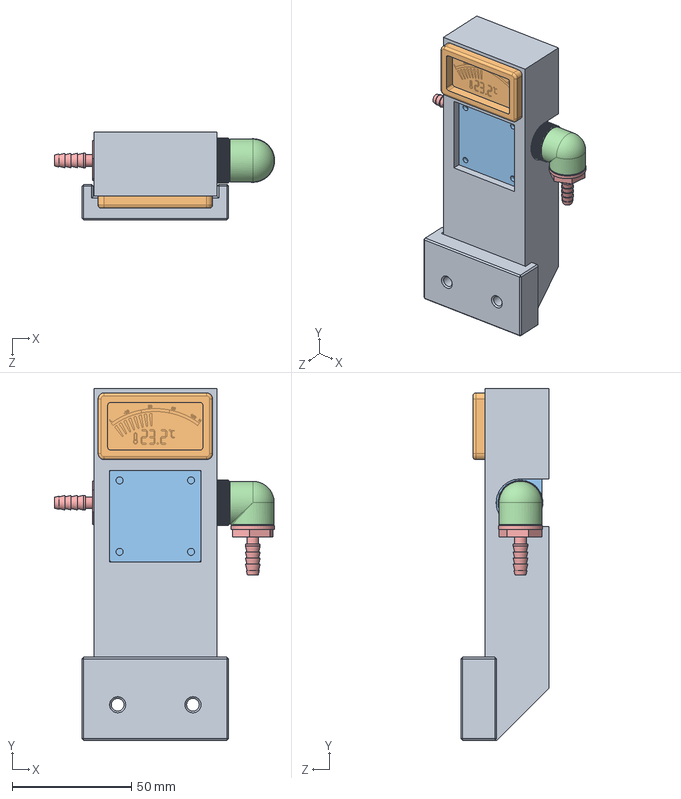
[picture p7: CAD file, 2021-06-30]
Solidworks/Sub Assemblies/Flow_Temp_Indicator_ASMB.SLDASM
92.5 x 147.8 x 37.0 mm
Flow Meter And Temp Gauge
Fosa Pointer Display Thermometer
Fosa G14 Flow Meter
EK-AF Angled 90deg G1_4
G14x6mm_Barb x 2

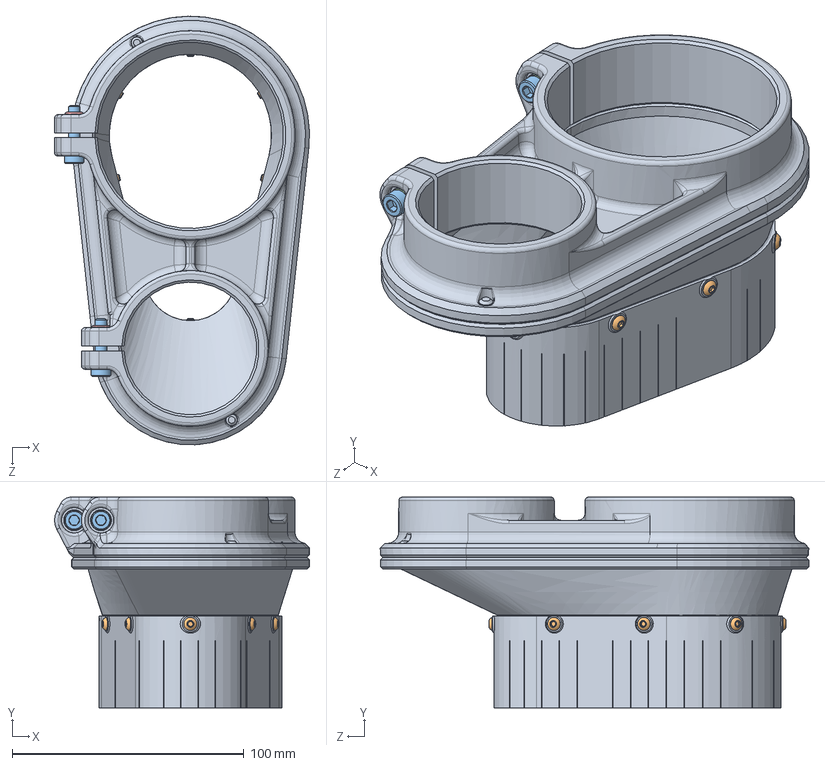
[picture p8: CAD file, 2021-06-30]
Solidworks/Sub Assemblies/Dust_Shoe.SLDASM
110.1 x 91.0 x 185.0 mm
Dust_Shoe
Trimcraft M3 BSC x 8
5mm_SCS_SST x 2
5mm_Washer_SST x 2
Trimcraft M5 Nylock Nut x 2
8mm x 3mm Neodymium Magnet x 20

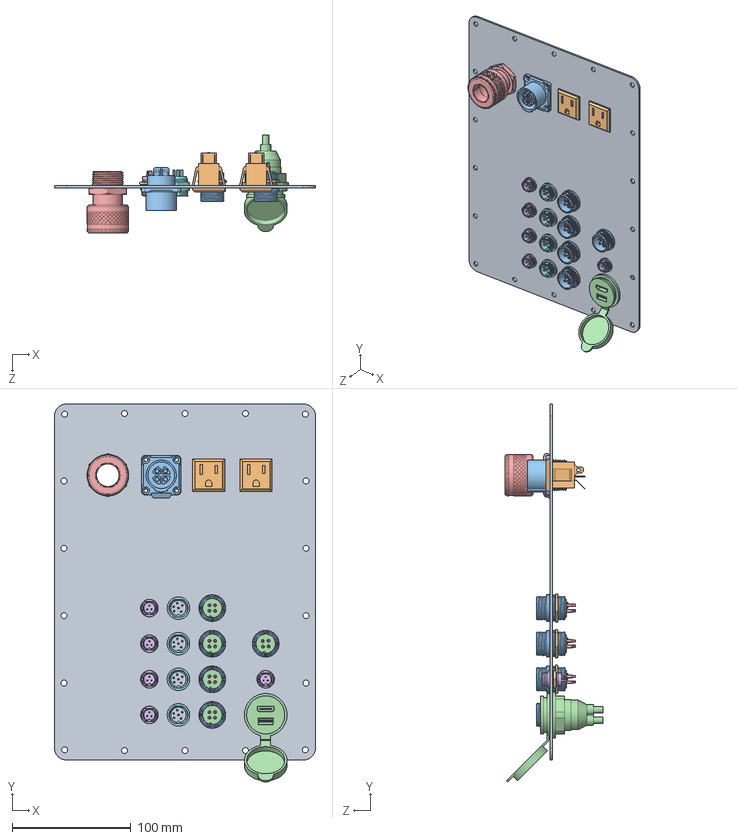
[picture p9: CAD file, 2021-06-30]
Solidworks/Sub Assemblies/Gland Plate Assembly.SLDASM
220.0 x 318.5 x 82.8 mm
Controller Gland Plate
nut x 5
upper sheath x 5
Inner plastic x 5
needle x 20
GX12-3P x 5
Nut M12x0.75 H=1.8mm v2 x 5
GX16-6 x 4
Acetal x 4
Female US 3 Pin Power Socket Plug Panel Mount x 2
CNLINKO LP24 4pin Connector
BATIGE USB3_HDMI_Panel_Mount
7529K191_STRAIGHT CORD GRIP

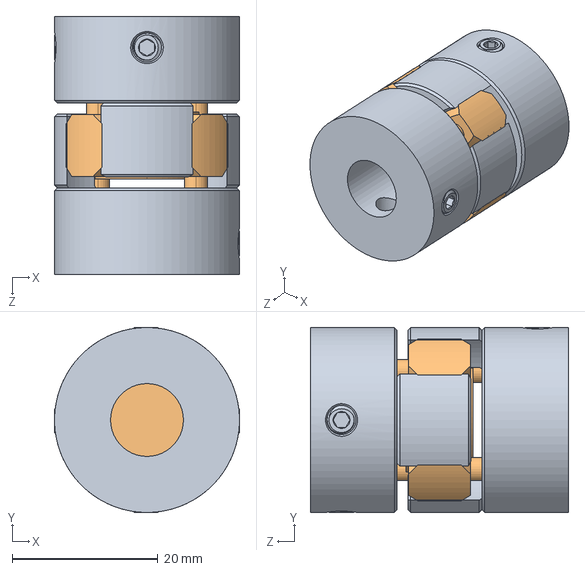
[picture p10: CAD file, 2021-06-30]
Solidworks/Hardware/Shaft Coupling (3 piece).SLDASM
25.4 x 25.4 x 35.4 mm
9939T321_VIBRATE-DAMPING PRECISION FLEXIBLE SHAFT COUPLING x 2
9845T140_VIBRATE-DAMPING PRECISION FLEXIBLE SHAFT CPLG

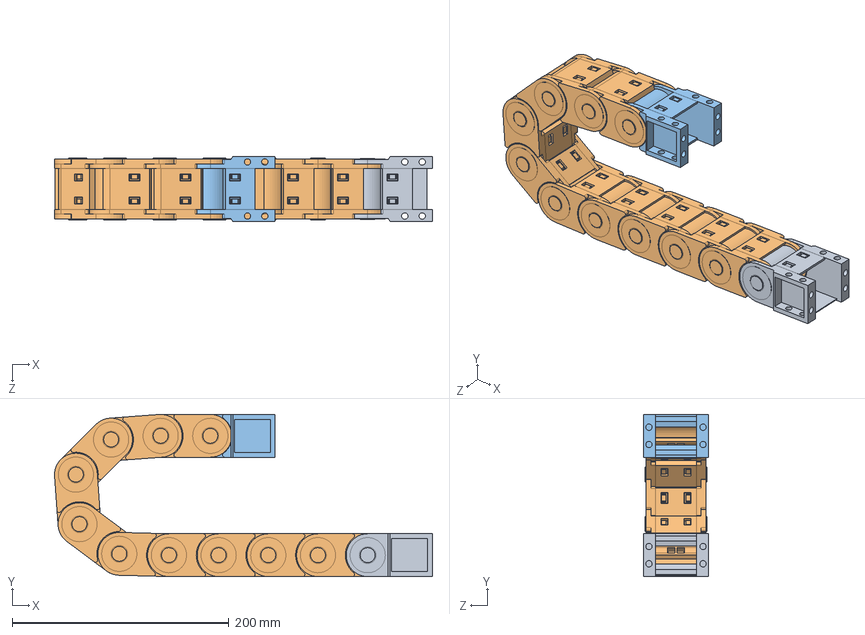
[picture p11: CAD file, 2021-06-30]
Solidworks/Sub Assemblies/H25 (25x38mm Drag Chain).SLDASM
348.5 x 149.5 x 59.9 mm
H25-EndLink1 (25x38_ID_Drag_Chain)
H25-CenterLink (25x38_ID_Drag_Chain) x 10
H25-EndLink2 (25x38_ID_Drag_Chain)

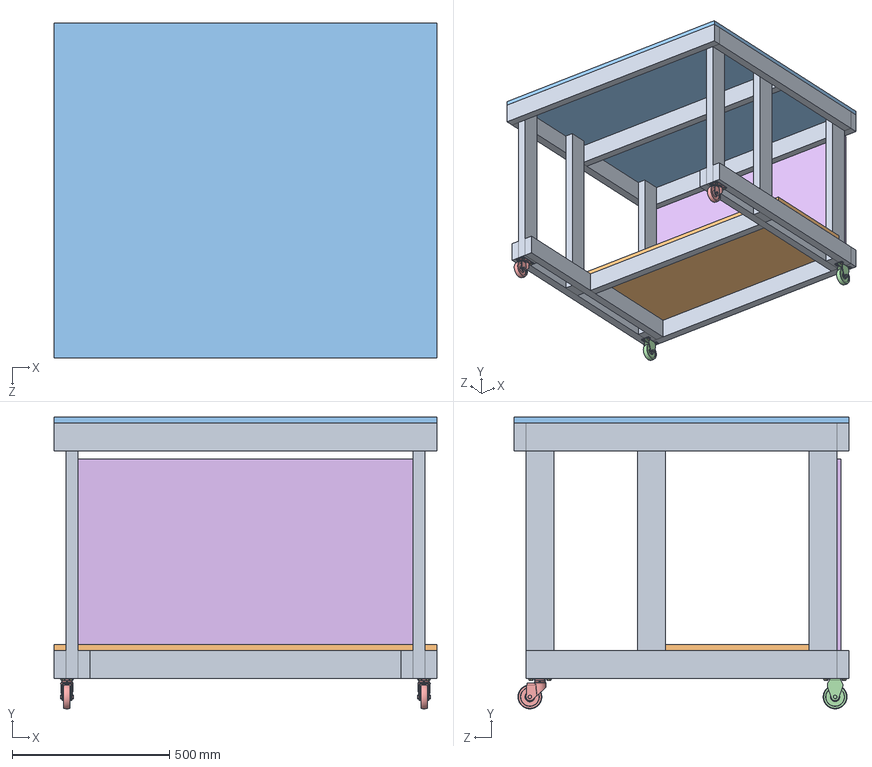
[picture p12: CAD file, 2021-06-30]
Solidworks/Wood Base/Workbench.sldasm
1219.2 x 928.7 x 1066.8 mm
2x4_Frame
Workbench Lower Shelf
Workbench_Top
2406T340_MIGHTY-LITE CASTER x 2
2406T290_MIGHTY-LITE CASTER x 2
Shelf Back Panel
0.25in x 1.125in SST Lag Screw x 16

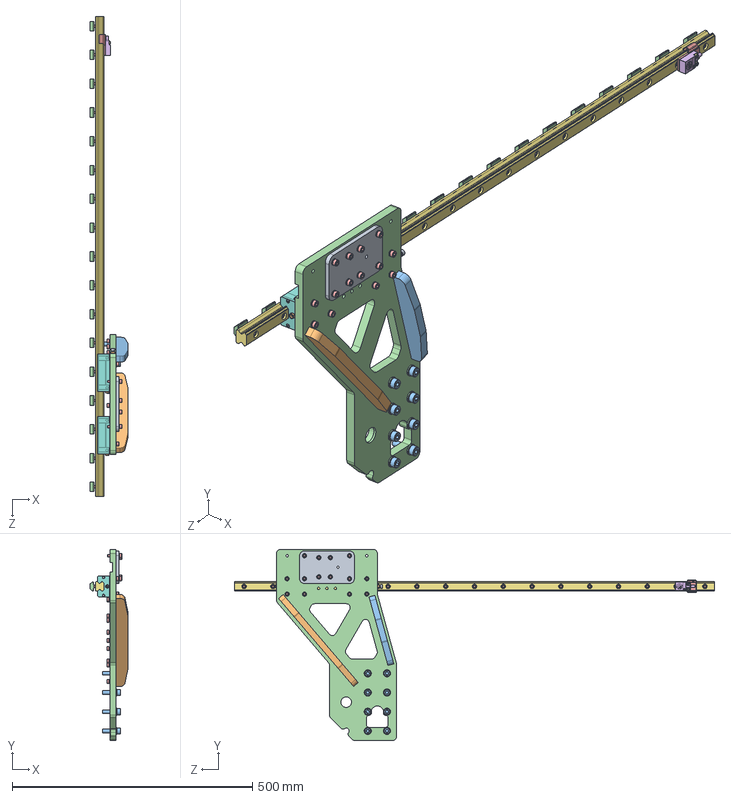
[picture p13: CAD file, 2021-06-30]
Solidworks/Sub Assemblies/Y Axis ASMB (Mirror).sldasm
79.6 x 398.0 x 1000.0 mm
Y-Axis_Ballscrew_Connection_Plate
Gantry Rib1
Gantry Rib2
MirrorGantry_Riser
Endstop Rail Mount
TL-W5MC1 (NO NPN Proximity Switch)
90751A112_METRIC FINE-THREAD 18-18 SS SOCKET HEAD SCREW x 2
93285A112_CONFORMABLE SOFT NYLON-TIP SET SCREW
91290A238_BLACK-OXIDE CLASS 12.9 SOCKET HEAD CAP SCREW
91828A241_TYPE 18-8 STAINLESS STEEL HEX NUT
8mm_SCS_SST x 8
8mm_Washer_SST x 8
5mm_SCS_SST x 41
5mm_Washer_SST x 24
HGR20R LINEAR GUIDE RAIL, CONFIGURABLE
HGH20CAZ0C, BLOCK, MIDSECTION x 2
HGH20CAZ0C, SCREW HEAD x 8
2421K310_FLUSH-STYLE GREASE FITTING x 2
98689A114_GENERAL PURPOSE 18-8 STAINLESS STEEL WASHER x 17
M5_Tnut_40Series-Profile x 17

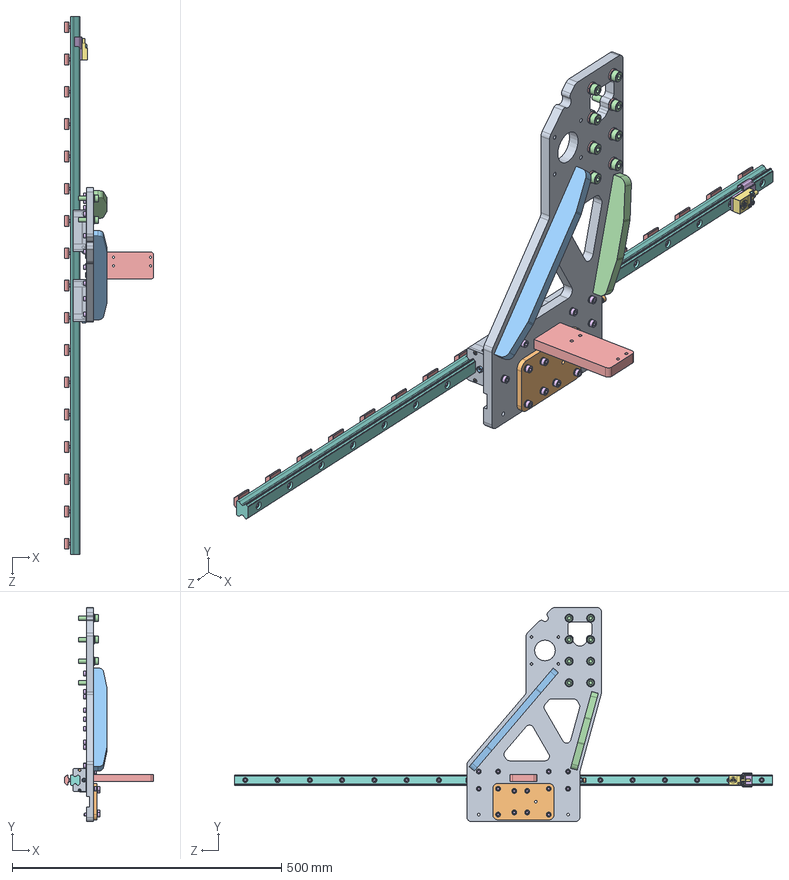
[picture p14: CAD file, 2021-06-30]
Solidworks/Sub Assemblies/Y Axis ASMB.sldasm
166.2 x 398.0 x 1000.0 mm
Gantry_Riser
Y-Axis_Ballscrew_Connection_Plate
Gantry Rib1
Gantry Rib2
Drag Chain Mount (Y Axis)
Endstop Rail Mount
TL-W5MC1 (NO NPN Proximity Switch)
90751A112_METRIC FINE-THREAD 18-18 SS SOCKET HEAD SCREW x 2
93285A112_CONFORMABLE SOFT NYLON-TIP SET SCREW
91290A238_BLACK-OXIDE CLASS 12.9 SOCKET HEAD CAP SCREW
91828A241_TYPE 18-8 STAINLESS STEEL HEX NUT
8mm_SCS_SST x 8
8mm_Washer_SST x 8
5mm_SCS_SST x 44
5mm_Washer_SST x 27
HGR20R LINEAR GUIDE RAIL, CONFIGURABLE
HGH20CAZ0C, BLOCK, MIDSECTION x 2
HGH20CAZ0C, SCREW HEAD x 8
2421K310_FLUSH-STYLE GREASE FITTING x 2
98689A114_GENERAL PURPOSE 18-8 STAINLESS STEEL WASHER x 17
M5_Tnut_40Series-Profile x 17

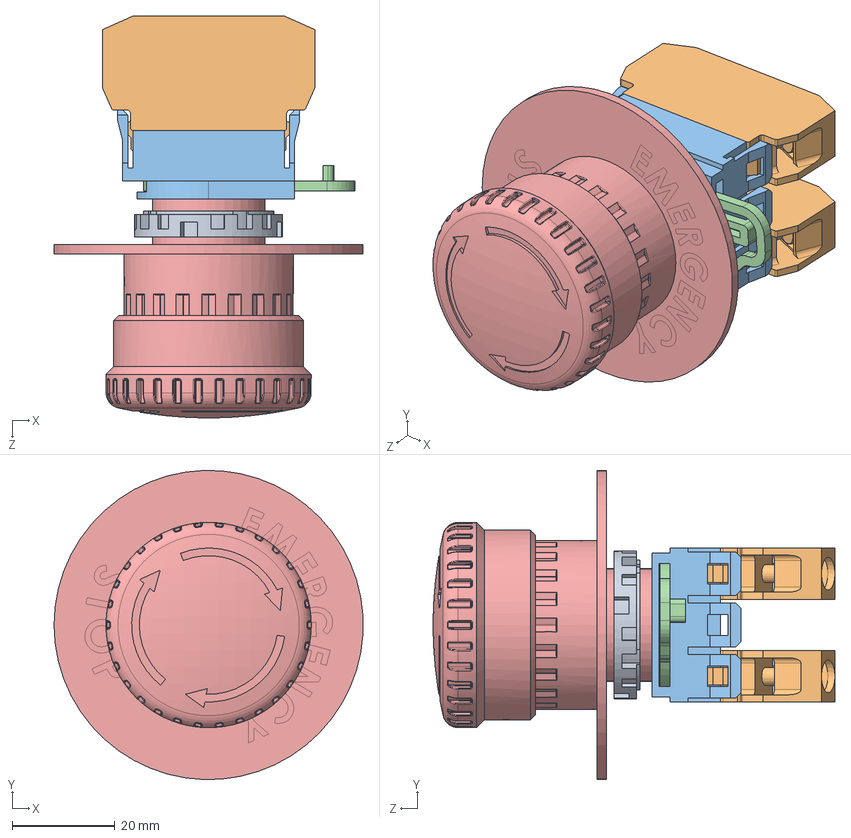
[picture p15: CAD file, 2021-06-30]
Solidworks/Electrical/YW1B-V4E11R EMERGENCY STOP (IDEC).SLDASM
60.2 x 60.2 x 78.3 mm
YW1B-V4E02R EMERGENCY STOP (IDEC)-1
YW1B-V4E02R EMERGENCY STOP (IDEC)-4 x 2
YW1B-V4E02R EMERGENCY STOP (IDEC)-2
YW1B-V4E02R EMERGENCY STOP (IDEC)-3
YW1B-V4E02R EMERGENCY STOP (IDEC)-5

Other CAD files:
Solidworks/Sub Assemblies/Bucket Dust Cyclone/5Gallon_Pail_Dust_Cyclone.SLDASM
Solidworks/Sub Assemblies/X Axis Drag Chain ASMB.sldasm
Solidworks/Sub Assemblies/Z Axis Drag Chain ASMB.sldasm
Solidworks/Sub Assemblies/Y Axis Dragchain.sldasm
DWG Prints/LCNC_BA.DWG
DWG Prints/LCNC_BC.DWG
DWG Prints/LCNC_BF.DWG
DWG Prints/LCNC_CP1.DWG
DWG Prints/LCNC_CP2.DWG
DWG Prints/LCNC_CP3.DWG
DWG Prints/LCNC_CP4.DWG
DWG Prints/LCNC_DC.DWG
DWG Prints/LCNC_DG.DWG
DWG Prints/LCNC_DU.DWG
DWG Prints/LCNC_GP1.DWG
DWG Prints/LCNC_GP2.DWG
DWG Prints/LCNC_GR.DWG
DWG Prints/LCNC_MP1.DWG
DWG Prints/LCNC_MP2.DWG
DWG Prints/LCNC_NP.DWG
DWG Prints/LCNC_SP.DWG
DWG Prints/LCNC_SR.DWG
DWG Prints/LCNC_TLA.DWG
DWG Prints/LCNC_WB1.DWG
DWG Prints/LCNC_WB2.DWG
DWG Prints/LCNC_WB3.DWG
DWG Prints/LCNC_XA.DWG
DWG Prints/LCNC_XB.DWG
DWG Prints/LCNC_XP.DWG
DWG Prints/LCNC_YE.DWG
DWG Prints/LCNC_YR1.DWG
DWG Prints/LCNC_YR2.DWG
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

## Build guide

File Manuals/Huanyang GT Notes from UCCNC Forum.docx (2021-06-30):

From: Chmexd5633 here http://www.forum.cncdrive.com/viewtopic.php?f=14&t=481&start=190

"Make sure you have your settings on the vfd

P0.00=0

P0.01=2

P0.02=0

P0.03=400

P0.04=400

P0.05=133.33 thats my preference

P0.06=133.33 not sure what I'm supposed to have here?? Someone help on this, I know its initial frequency reference.

P0.07=0

P0.08=0

P0.09=0

P0.10=0

P0.11=10

P0.12=10

P0.13=0 not sure if this is what everyone needs, I suspect my motor wiring is backwards, so that why in the Modbusez (spindle on cw and spindle on ccw might be backwards or opposite than yours, you will find out when you run it you might have to switch those 2)

P0.14=.5

P0.15=1

At one point I did decide to restore all settings to default on the vfd, that changed the settings on the vfd serial communications. Make sure your serial communications are as follows:

PC.00=001

PC.01=3

PC.02=00

PC.03=005

PC.04=0

PC.05=1

PC.06=000”

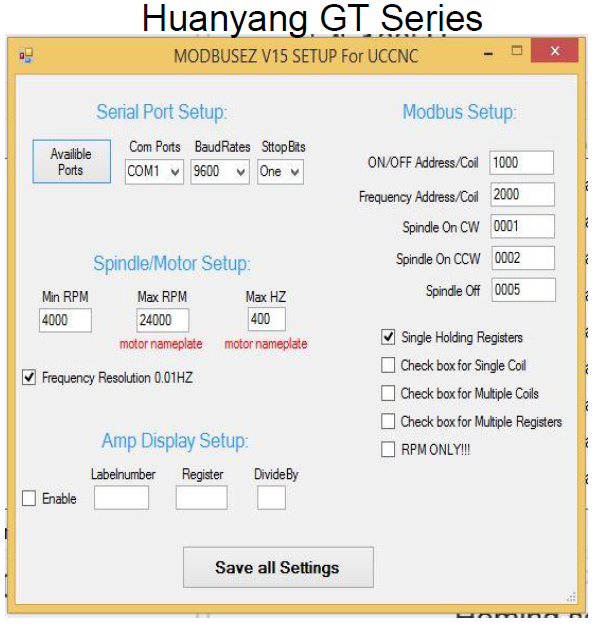
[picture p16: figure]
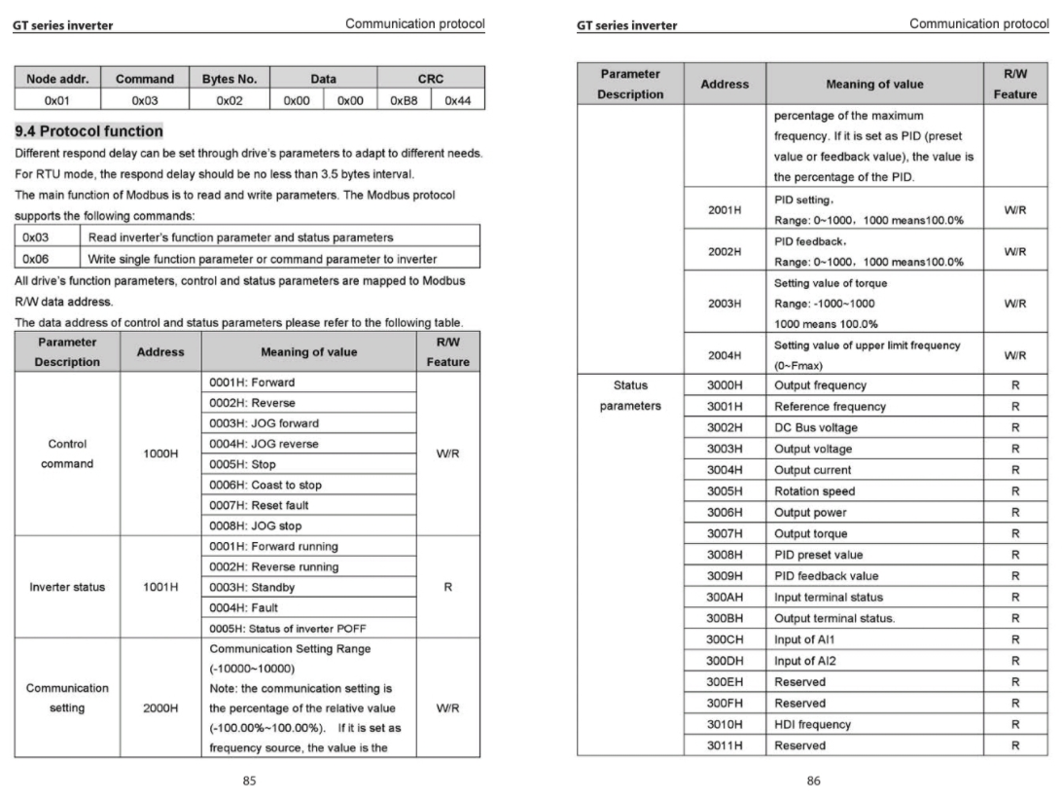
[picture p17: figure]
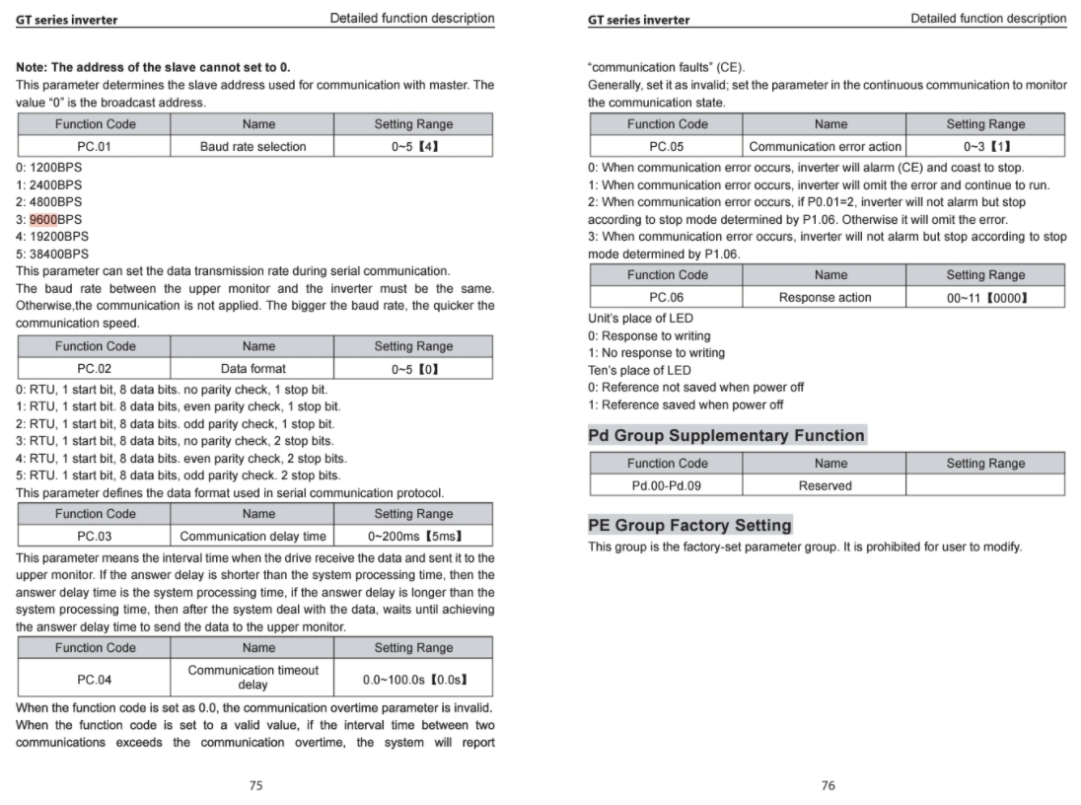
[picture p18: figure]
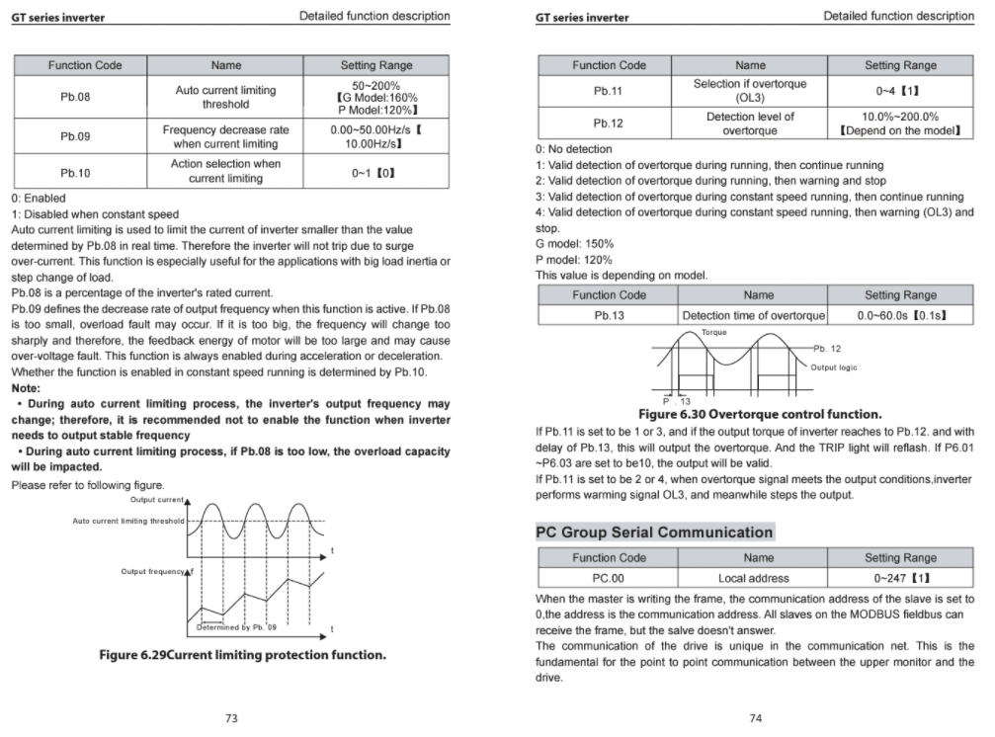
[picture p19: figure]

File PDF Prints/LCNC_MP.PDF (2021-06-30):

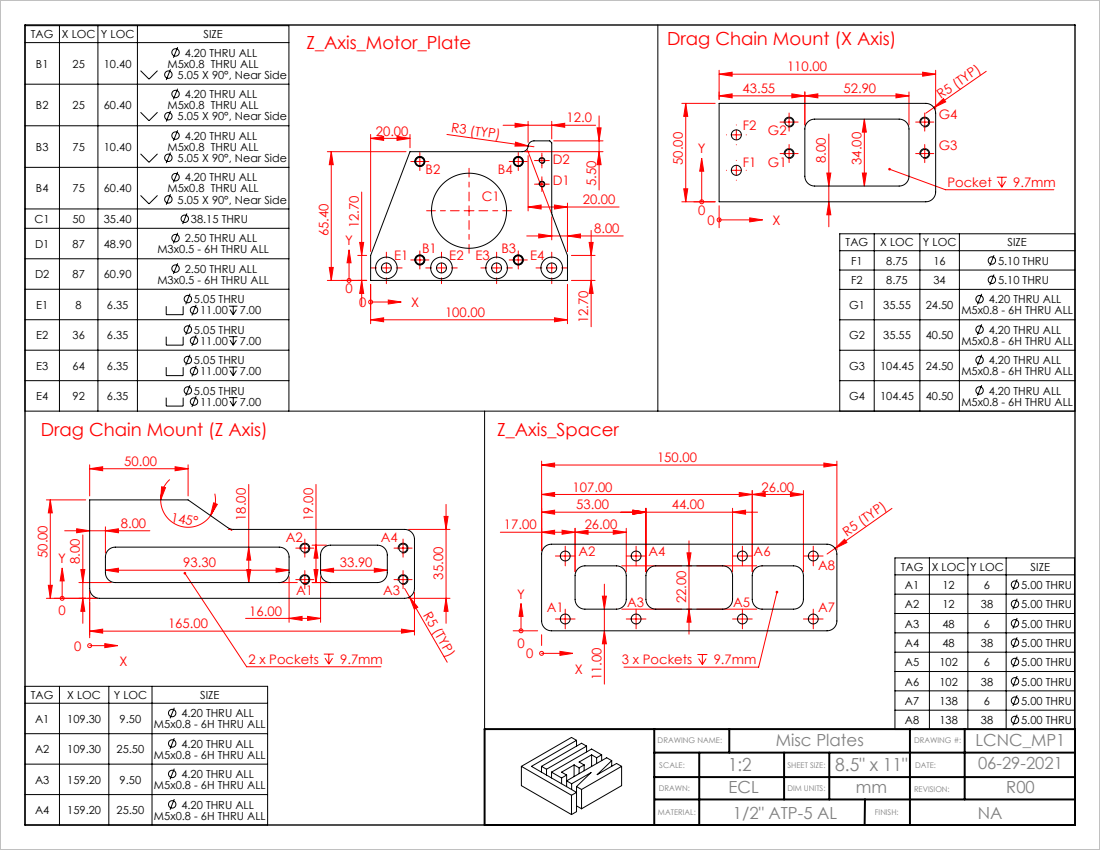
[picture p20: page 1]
R3 (TYP); R5 (TYP); Pocket 9.7mm; 3 x Pockets 9.7mm; 2 x Pockets 9.7mm; 5.05 THRU; 4.20 THRU ALL; M5x0.8 - 6H THRU ALL; 5.00 THRU

TAG | X LOC | Y LOC | SIZE | Z_Axis_Motor_Plate | Drag Chain Mount (X Axis) 110.00
B1 | 25 | 10.40 | 4.20 THRU ALL M5x0.8 THRU ALL 5.05 X 90°, Near Side

B2 | 25 | 60.40 | 4.20 THRU ALL M5x0.8 THRU ALL 5.05 X 90°, Near Side

B3 | 75 | 10.40 | 4.20 THRU ALL M5x0.8 THRU ALL 5.05 X 90°, Near Side

B4 | 75 | 60.40 | 4.20 THRU ALL M5x0.8 THRU ALL 5.05 X 90°, Near Side

C1 | 50 | 35.40 | 38.15 THRU
D1 | 87 | 48.90 | 2.50 THRU ALL M3x0.5 - 6H THRU ALL

TAG | X LOC | Y LOC | SIZE
F1 | 8.75 | 16 | 5.10 THRU
F2 | 8.75 | 34 | 5.10 THRU

D2 | 87 | 60.90 | 2.50 THRU ALL M3x0.5 - 6H THRU ALL

Drag Chain Mount (Z Axis)

A1 | 12 | 6 | 5.00 THRU
A2 | 12 | 38 | 5.00 THRU
A3 | 48 | 6 | 5.00 THRU

A5 | 102 | 6 | 5.00 THRU
A6 | 102 | 38 | 5.00 THRU
A7 | 138 | 6 | 5.00 THRU
A8 | 138 | 38 | 5.00 THRU

A1 | 109.30 | 9.50 | 4.20 THRU ALL M5x0.8 - 6H THRU ALL

A2 | 109.30 | 25.50 | 4.20 THRU ALL M5x0.8 - 6H THRU ALL

DRAWING NAME: | Misc Plates | DRAWING #: | LCNC_MP1
SCALE: | 1:2 | SHEET SIZE: | 8.5" x 11" | DATE: | 06-29-2021
DRAWN: | ECL | DIM UNITS: | mm | REVISION: | R00
MATERIAL: | 1/2" ATP-5 AL | FINISH: | NA

A3 | 159.20 | 9.50 | 4.20 THRU ALL M5x0.8 - 6H THRU ALL

A4 | 159.20 | 25.50 | 4.20 THRU ALL M5x0.8 - 6H THRU ALL

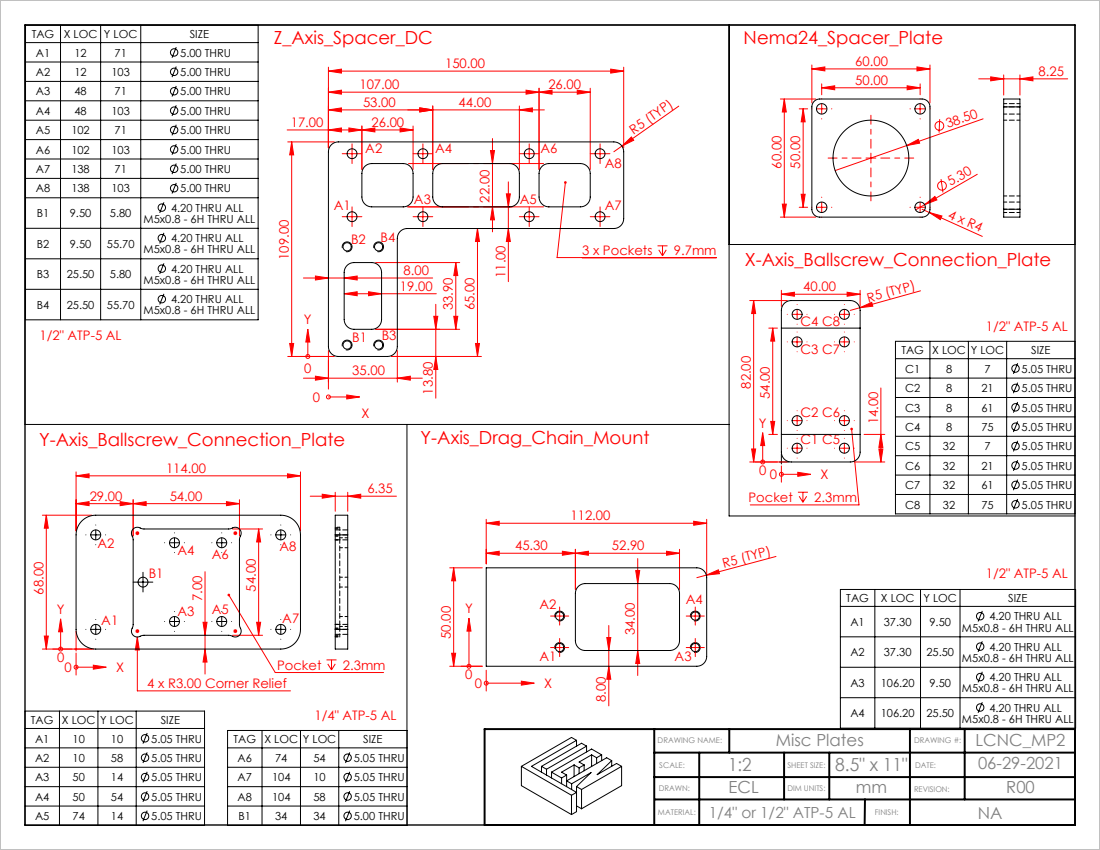
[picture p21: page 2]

TAG | X LOC | Y LOC | SIZE | Z_Axis_Spacer_DC 150.00 | Nema24_Spacer_Plate 60.00
A1 | 12 | 71 | 5.00 THRU
A2 | 12 | 103 | 5.00 THRU
A3 | 48 | 71 | 5.00 THRU
A4 | 48 | 103 | 5.00 THRU
A5 | 102 | 71 | 5.00 THRU
A6 | 102 | 103 | 5.00 THRU
A7 | 138 | 71 | 5.00 THRU
A8 | 138 | 103 | 5.00 THRU
B1 | 9.50 | 5.80 | 4.20 THRU ALL M5x0.8 - 6H THRU ALL

B2 | 9.50 | 55.70 | 4.20 THRU ALL M5x0.8 - 6H THRU ALL

B3 | 25.50 | 5.80 | 4.20 THRU ALL M5x0.8 - 6H THRU ALL

B4 | 25.50 | 55.70 | 4.20 THRU ALL M5x0.8 - 6H THRU ALL

TAG | X LOC | Y LOC | SIZE
C1 | 8 | 7 | 5.05 THRU
C2 | 8 | 21 | 5.05 THRU
C3 | 8 | 61 | 5.05 THRU
C4 | 8 | 75 | 5.05 THRU
C5 | 32 | 7 | 5.05 THRU
C6 | 32 | 21 | 5.05 THRU

Y-Axis_Ballscrew_Connection_Plate

A1 | 37.30 | 9.50 | 4.20 THRU ALL M5x0.8 - 6H THRU ALL

A2 | 37.30 | 25.50 | 4.20 THRU ALL M5x0.8 - 6H THRU ALL

A3 | 106.20 | 9.50 | 4.20 THRU ALL M5x0.8 - 6H THRU ALL

A4 | 106.20 | 25.50 | 4.20 THRU ALL M5x0.8 - 6H THRU ALL

SCALE: | 1:2 | SHEET SIZE: | 8.5" x 11" | DATE: | 06-29-2021
DRAWN: | ECL | DIM UNITS: | mm | REVISION: | R00
MATERIAL: | 1/4" or 1/2" ATP-5 AL | FINISH: | NA

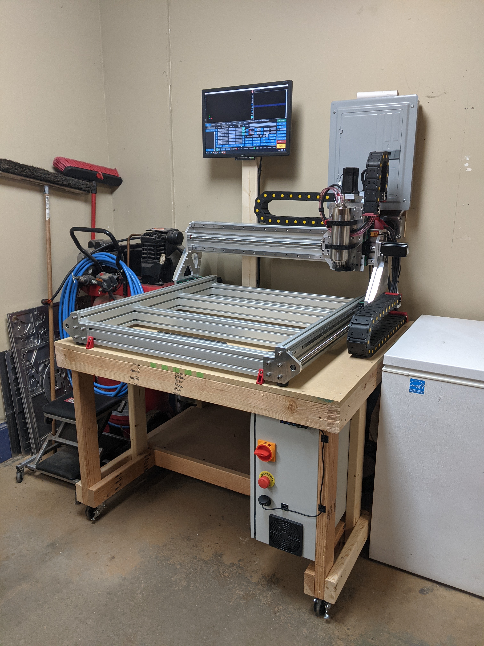
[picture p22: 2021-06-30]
Pictures and Videos/During Assembly/LienCNC_Picture (3).jpg

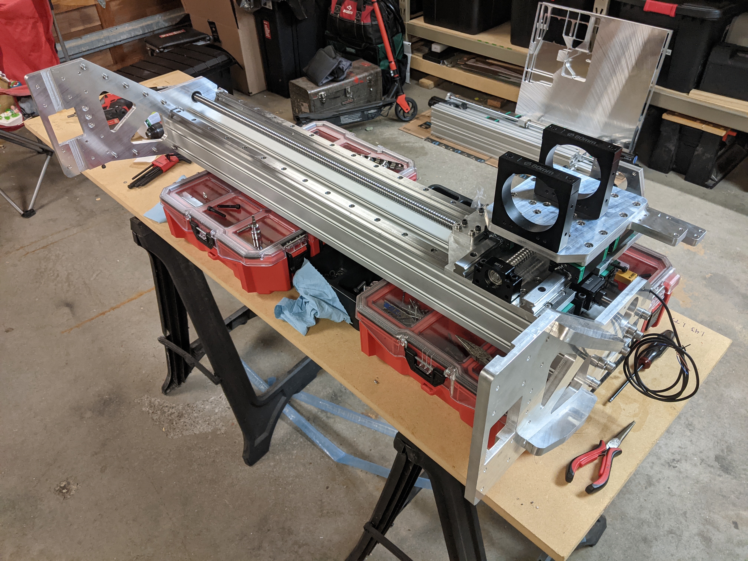
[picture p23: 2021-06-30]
Pictures and Videos/During Assembly/LienCNC_Picture (56).jpg

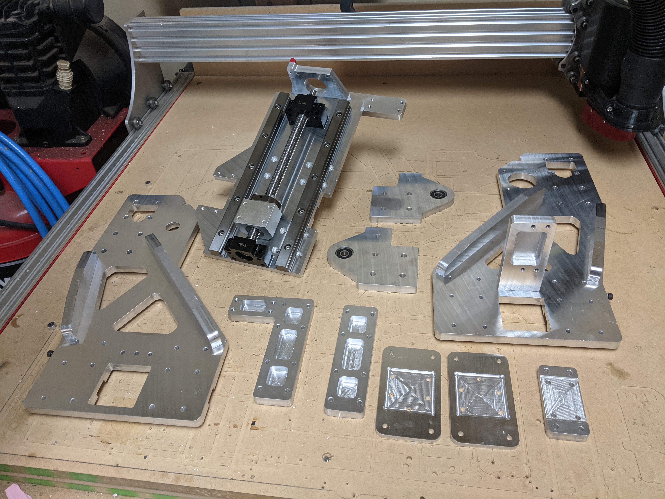
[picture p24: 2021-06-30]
Pictures and Videos/During Assembly/LienCNC_Picture (62).jpg

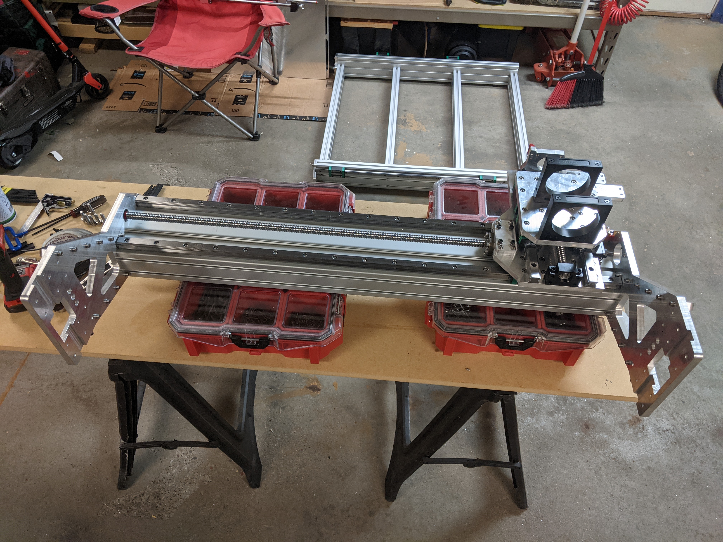
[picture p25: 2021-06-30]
Pictures and Videos/During Assembly/LienCNC_Picture (53).jpg

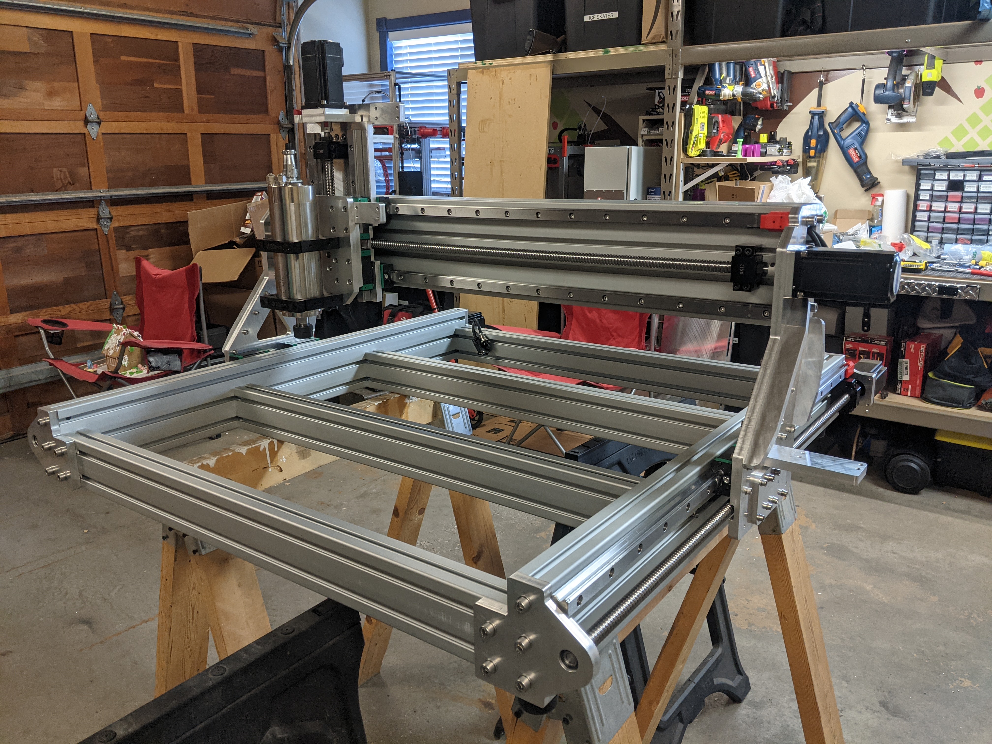
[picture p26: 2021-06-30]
Pictures and Videos/During Assembly/LienCNC_Picture (48).jpg

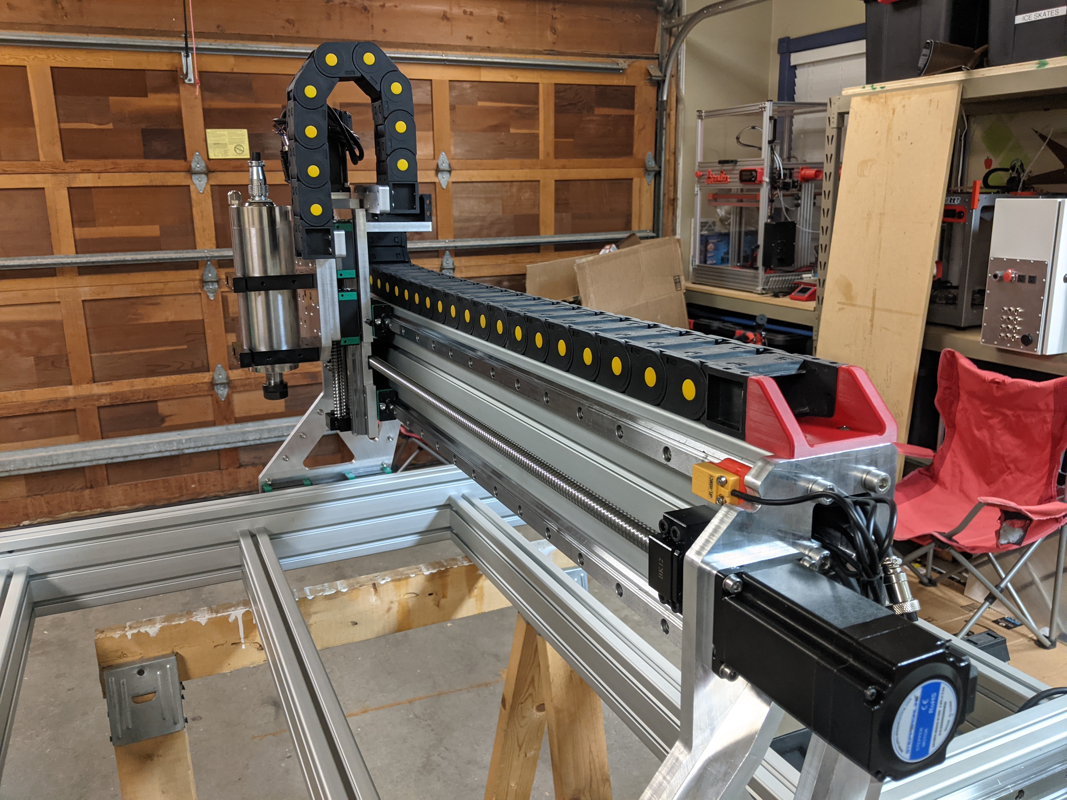
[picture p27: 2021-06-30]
Pictures and Videos/During Assembly/LienCNC_Picture (37).jpg

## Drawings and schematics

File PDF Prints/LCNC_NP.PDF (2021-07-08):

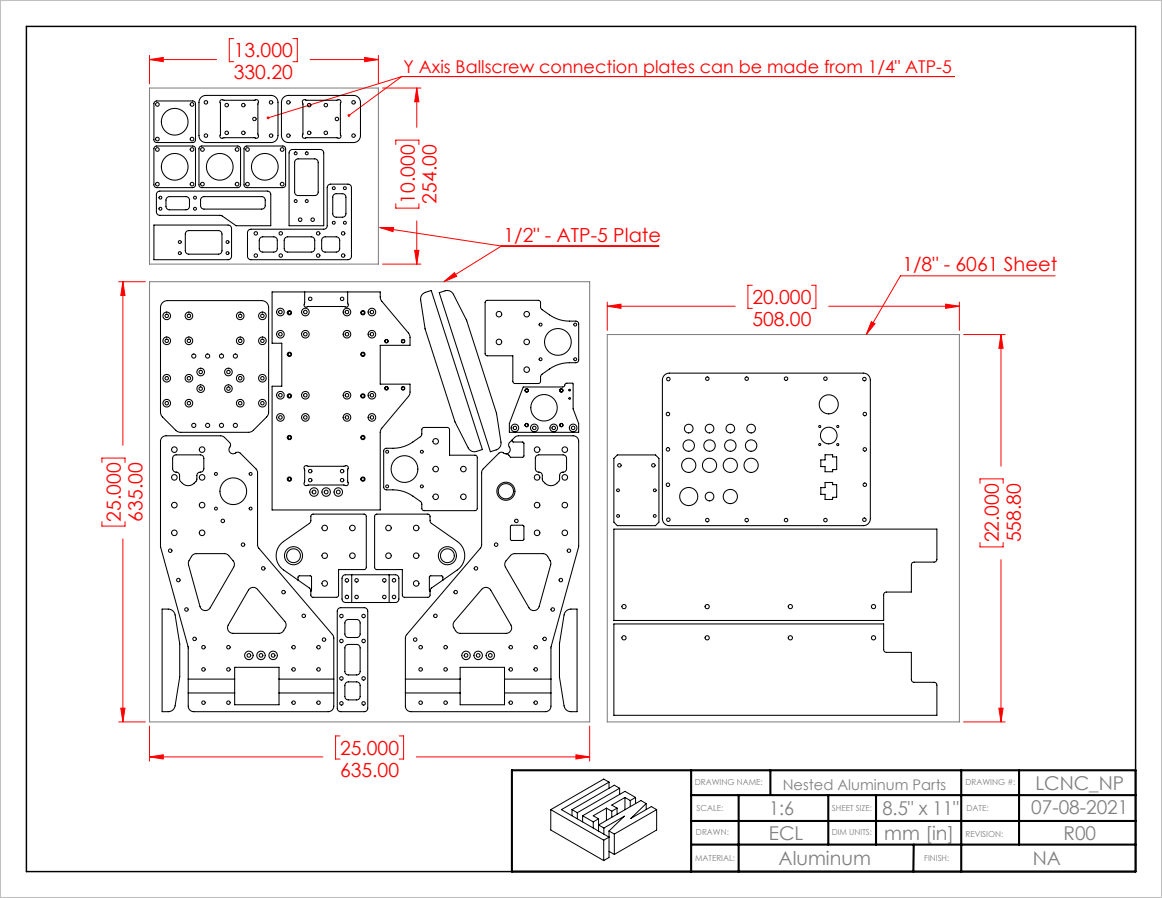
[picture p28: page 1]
1/8" - 6061 Sheet; 1/2" - ATP-5 Plate

Y Axis Ballscrew connection plates can be made from 1/4" ATP-5

DRAWING NAME: | Nested Aluminum Parts | DRAWING #: | LCNC_NP
SCALE: | 1:6 | SHEET SIZE: | 8.5" x 11" | DATE: | 07-08-2021
DRAWN: | ECL | DIM UNITS: | mm [in] | REVISION: | R00
MATERIAL: | Aluminum | FINISH: | NA

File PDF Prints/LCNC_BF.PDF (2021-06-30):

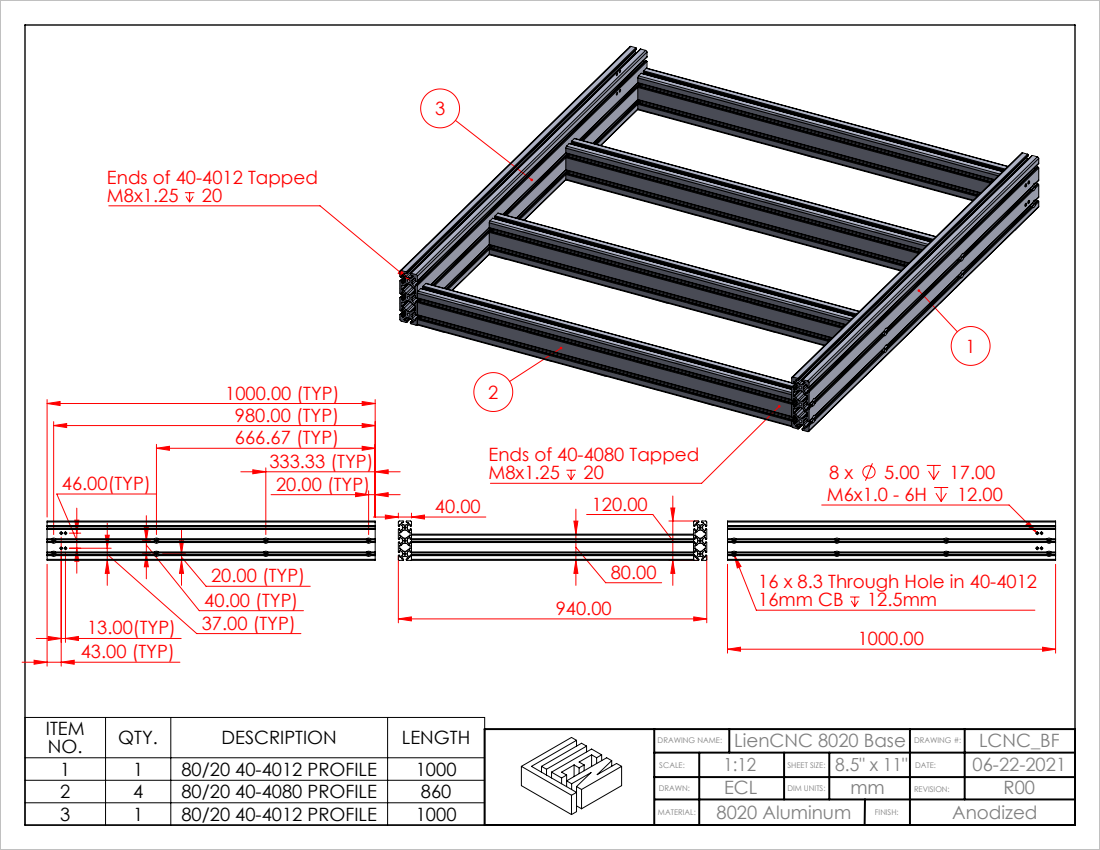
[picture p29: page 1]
Ends of 40-4080 Tapped M8x1.25 20; 20.00 (TYP); 333.33 (TYP); 666.67 (TYP); 980.00 (TYP); 1000.00 (TYP); 43.00 (TYP); 13.00(TYP) 37.00 (TYP); 20.00 (TYP) 40.00 (TYP)

Ends of 40-4012 Tapped

16 x 8.3 Through Hole in 40-4012

ITEM NO. | QTY. | DESCRIPTION | LENGTH
1 | 1 | 80/20 40-4012 PROFILE | 1000
2 | 4 | 80/20 40-4080 PROFILE | 860 | DRAWN: | ECL | DIM UNITS: | mm | REVISION: | R00
3 | 1 | 80/20 40-4012 PROFILE | 1000 | MATERIAL: | 8020 Aluminum | FINISH: | Anodized

DRAWING NAME: | LienCNC 8020 Base | DRAWING #: | LCNC_BF
SCALE: | 1:12 | SHEET SIZE: | 8.5" x 11" | DATE: | 06-22-2021

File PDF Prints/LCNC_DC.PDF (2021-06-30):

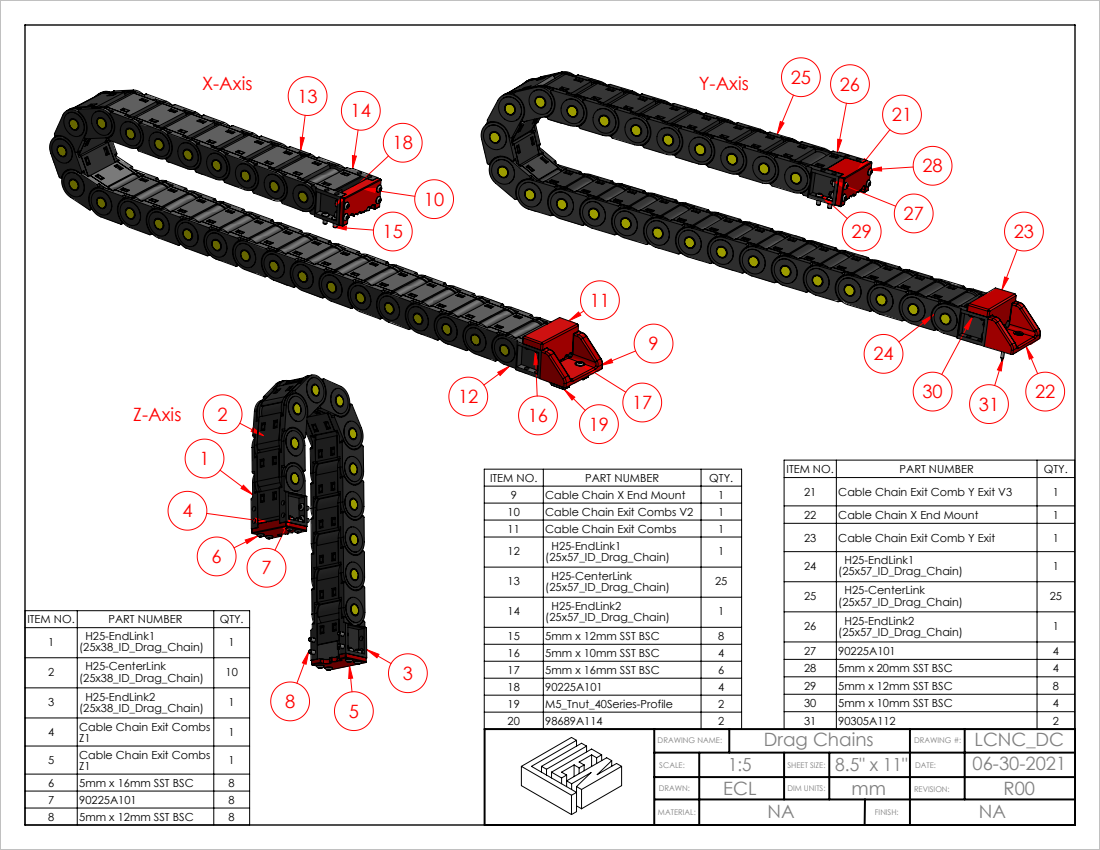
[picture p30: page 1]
ITEM NO.; PART NUMBER; QTY.; Cable Chain Exit Combs V2; 5mm x 12mm SST BSC; 5mm x 10mm SST BSC; 5mm x 16mm SST BSC; Cable Chain X End Mount; 5mm x 20mm SST BSC

ITEM NO. | PART NUMBER | QTY.
9 | Cable Chain X End Mount | 1

21 | Cable Chain Exit Comb Y Exit V3 | 1

11 | Cable Chain Exit Combs | 1
12 | H25-EndLink1 (25x57_ID_Drag_Chain) | 1

23 | Cable Chain Exit Comb Y Exit | 1
24 | H25-EndLink1 (25x57_ID_Drag_Chain) | 1

13 | H25-CenterLink (25x57_ID_Drag_Chain) | 25

25 | H25-CenterLink (25x57_ID_Drag_Chain) | 25

14 | H25-EndLink2 (25x57_ID_Drag_Chain) | 1

3 | H25-EndLink2 (25x38_ID_Drag_Chain) | 1

4 | Cable Chain Exit Combs Z1 | 1
5 | Cable Chain Exit Combs Z1 | 1
6 | 5mm x 16mm SST BSC | 8
7 | 90225A101 | 8
8 | 5mm x 12mm SST BSC | 8

DRAWING NAME: | Drag Chains | DRAWING #: | LCNC_DC
SCALE: | 1:5 | SHEET SIZE: | 8.5" x 11" | DATE: | 06-30-2021
DRAWN: | ECL | DIM UNITS: | mm | REVISION: | R00
MATERIAL: | NA | FINISH: | NA

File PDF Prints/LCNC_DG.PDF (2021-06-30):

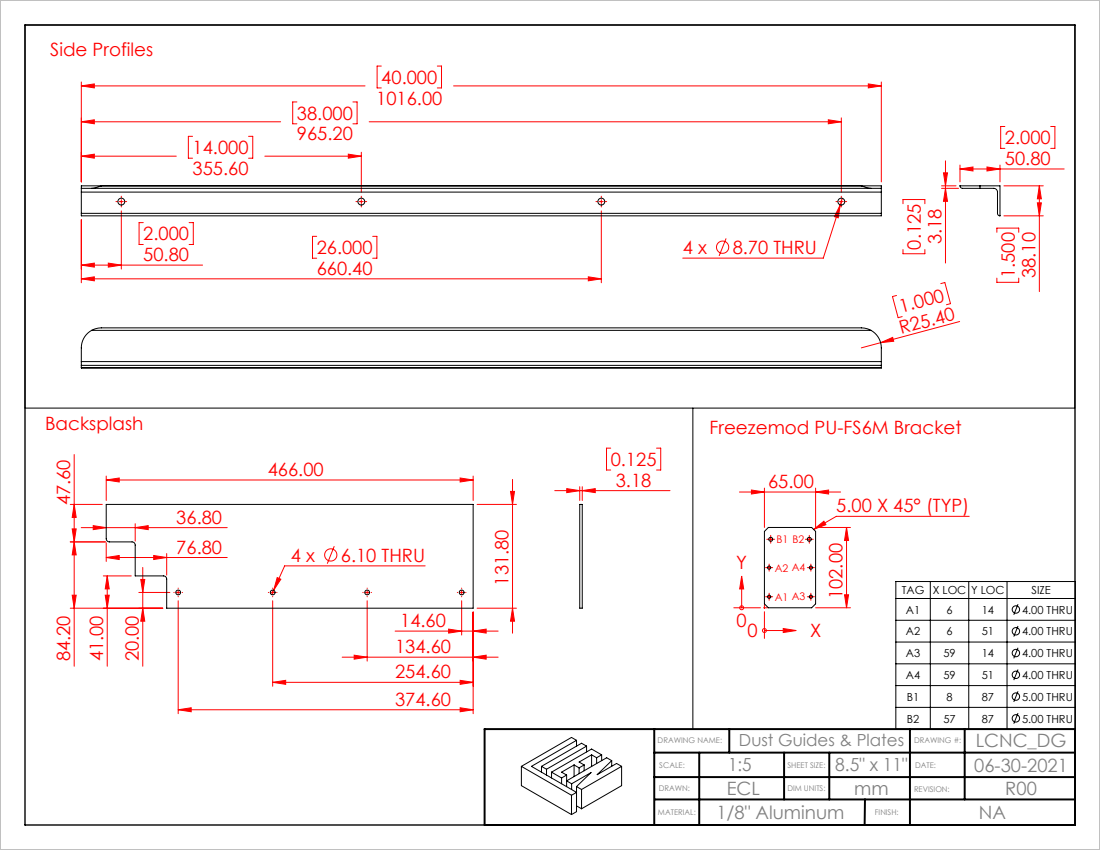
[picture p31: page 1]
4 x 8.70 THRU; 4 x 6.10 THRU; 5.00 X 45° (TYP); Side Profiles

Freezemod PU-FS6M Bracket

TAG | X LOC | Y LOC | SIZE
A1 | 6 | 14 | 4.00 THRU
A2 | 6 | 51 | 4.00 THRU
A3 | 59 | 14 | 4.00 THRU
A4 | 59 | 51 | 4.00 THRU
B1 | 8 | 87 | 5.00 THRU
B2 | 57 | 87 | 5.00 THRU

DRAWING NAME: | Dust Guides & Plates | DRAWING #: | LCNC_DG
SCALE: | 1:5 | SHEET SIZE: | 8.5" x 11" | DATE: | 06-30-2021
DRAWN: | ECL | DIM UNITS: | mm | REVISION: | R00
MATERIAL: | 1/8" Aluminum | FINISH: | NA

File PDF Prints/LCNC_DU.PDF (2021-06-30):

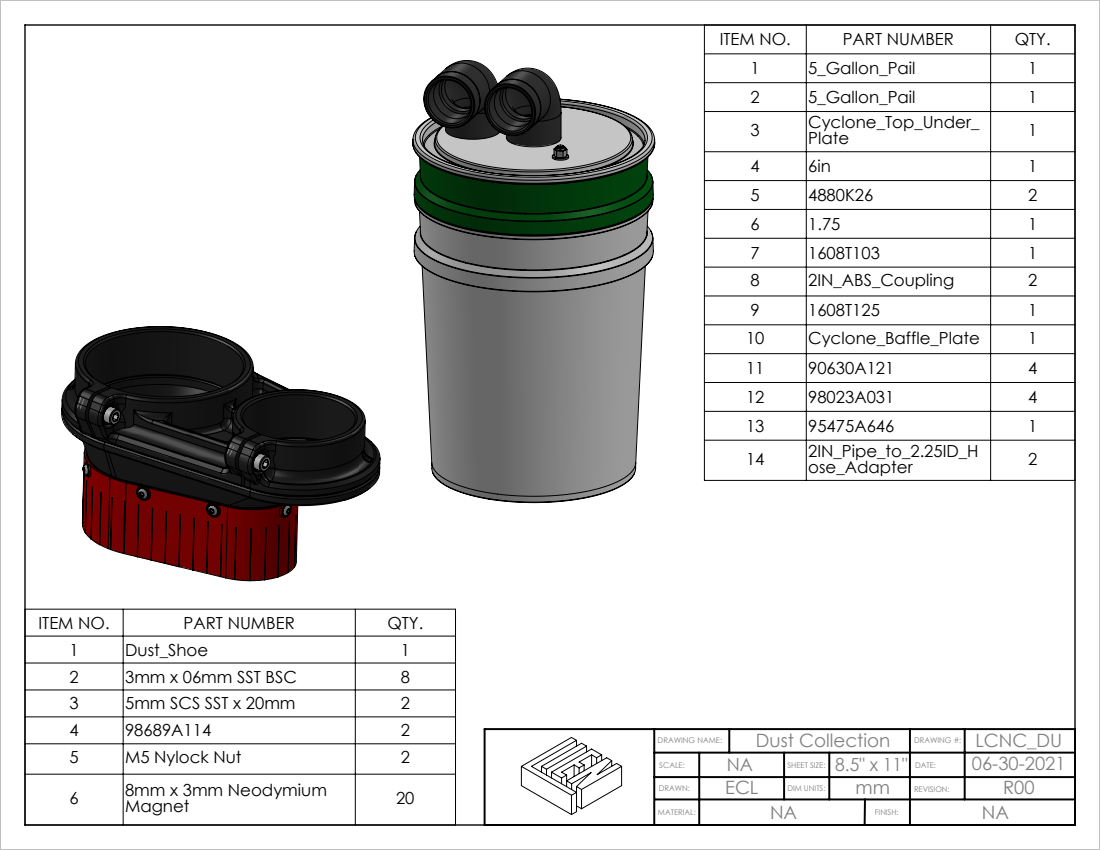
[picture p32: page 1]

ITEM NO. | PART NUMBER | QTY.
1 | 5_Gallon_Pail | 1
2 | 5_Gallon_Pail | 1
3 | Cyclone_Top_Under_ Plate | 1

4 | 6in | 1
5 | 4880K26 | 2
6 | 1.75 | 1
7 | 1608T103 | 1
8 | 2IN_ABS_Coupling | 2
9 | 1608T125 | 1
10 | Cyclone_Baffle_Plate | 1
11 | 90630A121 | 4
12 | 98023A031 | 4
13 | 95475A646 | 1
14 | 2IN_Pipe_to_2.25ID_H ose_Adapter | 2

1 | Dust_Shoe | 1
2 | 3mm x 06mm SST BSC | 8
3 | 5mm SCS SST x 20mm | 2
4 | 98689A114 | 2
5 | M5 Nylock Nut | 2
6 | 8mm x 3mm Neodymium Magnet | 20

DRAWING NAME: | Dust Collection | DRAWING #: | LCNC_DU
SCALE: | NA | SHEET SIZE: | 8.5" x 11" | DATE: | 06-30-2021
DRAWN: | ECL | DIM UNITS: | mm | REVISION: | R00
MATERIAL: | NA | FINISH: | NA

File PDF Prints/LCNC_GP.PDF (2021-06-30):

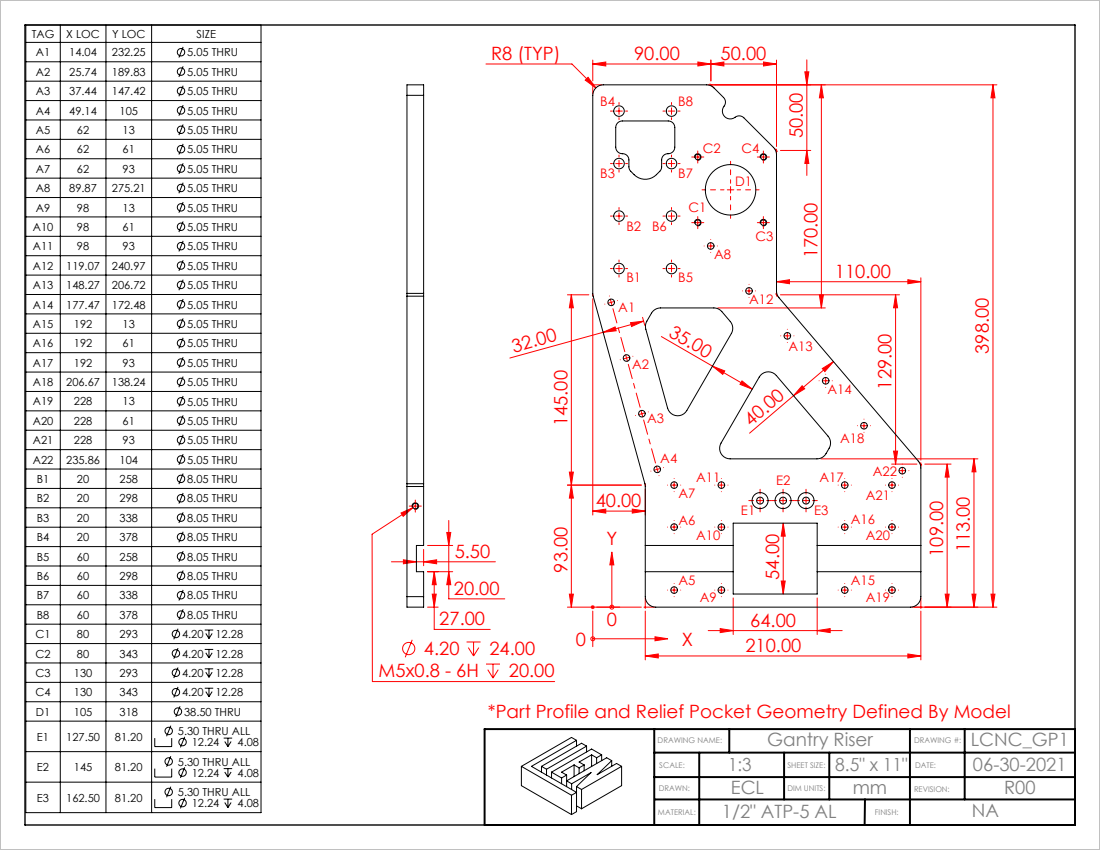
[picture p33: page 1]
R8 (TYP); 5.30 THRU ALL; SHEET SIZE:

TAG | X LOC | Y LOC | SIZE | 90.00 50.00
A1 | 14.04 | 232.25 | 5.05 THRU
A2 | 25.74 | 189.83 | 5.05 THRU
A3 | 37.44 | 147.42 | 5.05 THRU
A4 | 49.14 | 105 | 5.05 THRU
A5 | 62 | 13 | 5.05 THRU
A6 | 62 | 61 | 5.05 THRU
A7 | 62 | 93 | 5.05 THRU
A8 | 89.87 | 275.21 | 5.05 THRU
A9 | 98 | 13 | 5.05 THRU
A10 | 98 | 61 | 5.05 THRU
A11 | 98 | 93 | 5.05 THRU
A12 | 119.07 | 240.97 | 5.05 THRU
A13 | 148.27 | 206.72 | 5.05 THRU
A14 | 177.47 | 172.48 | 5.05 THRU
A15 | 192 | 13 | 5.05 THRU
A16 | 192 | 61 | 5.05 THRU
A17 | 192 | 93 | 5.05 THRU
A18 | 206.67 | 138.24 | 5.05 THRU
A19 | 228 | 13 | 5.05 THRU
A20 | 228 | 61 | 5.05 THRU
A21 | 228 | 93 | 5.05 THRU
A22 | 235.86 | 104 | 5.05 THRU
B1 | 20 | 258 | 8.05 THRU
B2 | 20 | 298 | 8.05 THRU
B3 | 20 | 338 | 8.05 THRU

B4 | 20 | 378 | 8.05 THRU
B5 | 60 | 258 | 8.05 THRU
B6 | 60 | 298 | 8.05 THRU
B7 | 60 | 338 | 8.05 THRU
B8 | 60 | 378 | 8.05 THRU
C1 | 80 | 293 | 4.20 12.28
C2 | 80 | 343 | 4.20 12.28
C3 | 130 | 293 | 4.20 12.28
C4 | 130 | 343 | 4.20 12.28
D1 | 105 | 318 | 38.50 THRU
E1 | 127.50 | 81.20 | 5.30 THRU ALL

*Part Profile and Relief Pocket Geometry Defined By Model

DRAWING NAME: | Gantry Riser | DRAWING #: | LCNC_GP1

DRAWN: | ECL | DIM UNITS: | mm | REVISION: | R00
MATERIAL: | 1/2" ATP-5 AL | FINISH: | NA

E3 | 162.50 | 81.20 | 5.30 THRU ALL

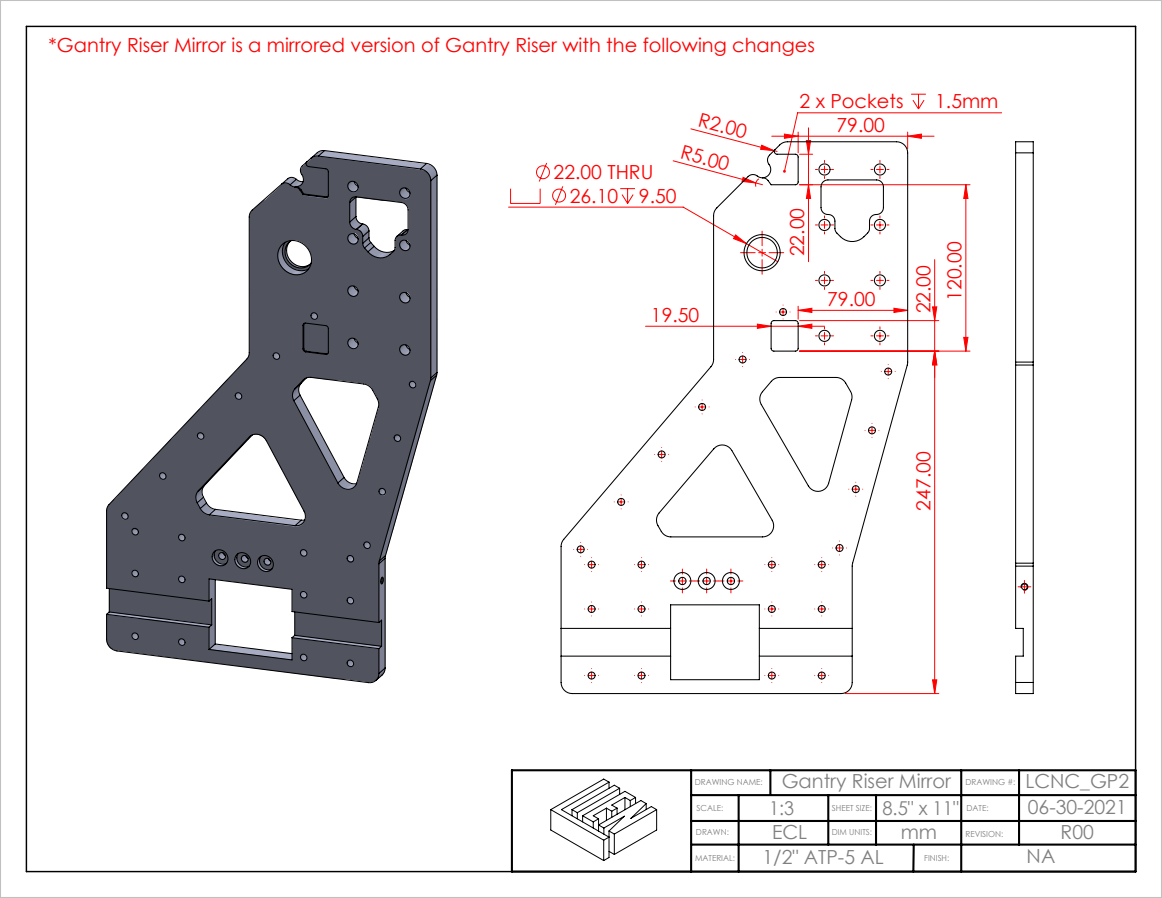
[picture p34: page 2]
22.00 THRU 26.10 9.50; 2 x Pockets 1.5mm

*Gantry Riser Mirror is a mirrored version of Gantry Riser with the following changes

DRAWING NAME: | Gantry Riser Mirror | DRAWING #: | LCNC_GP2
SCALE: | 1:3 | SHEET SIZE: | 8.5" x 11" | DATE: | 06-30-2021
DRAWN: | ECL | DIM UNITS: | mm | REVISION: | R00
MATERIAL: | 1/2" ATP-5 AL | FINISH: | NA

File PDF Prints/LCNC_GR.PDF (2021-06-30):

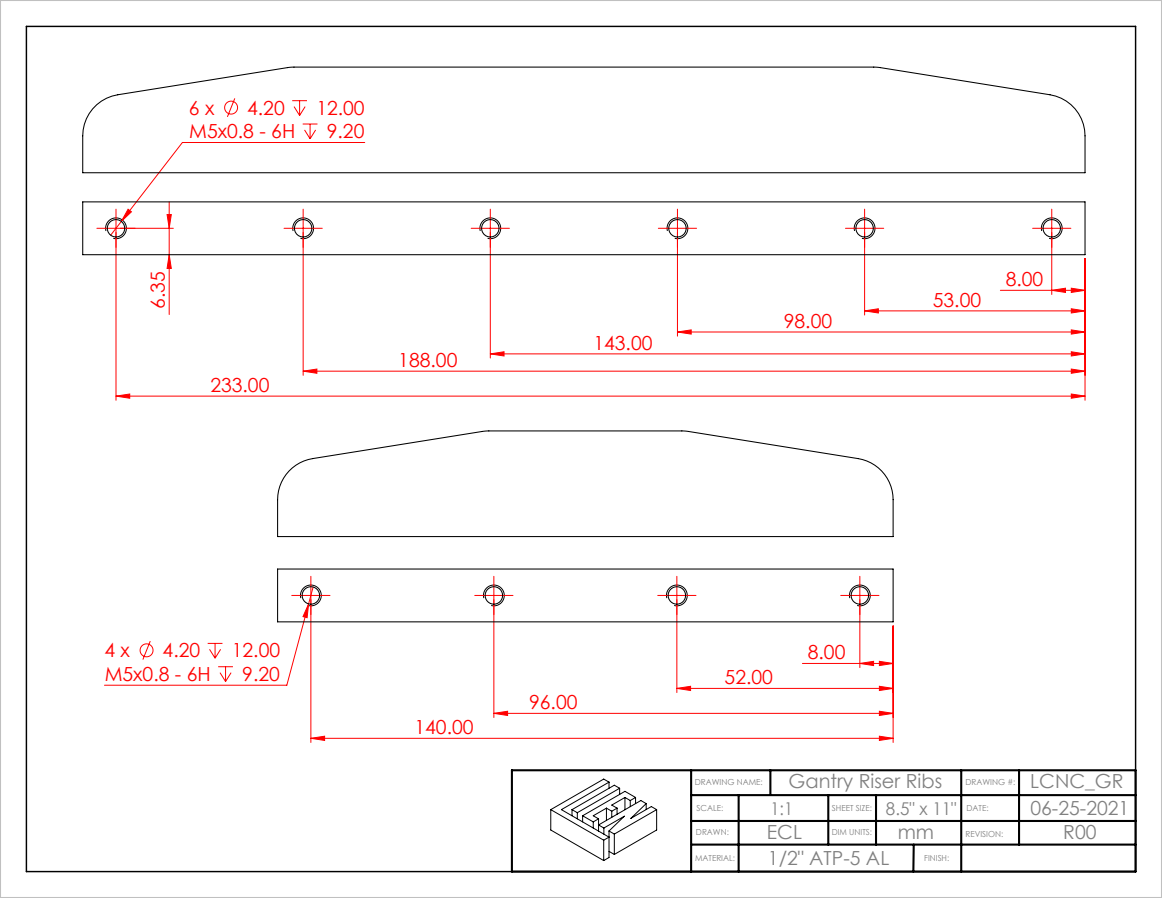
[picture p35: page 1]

DRAWING NAME: | Gantry Riser Ribs | DRAWING #: | LCNC_GR
SCALE: | 1:1 | SHEET SIZE: | 8.5" x 11" | DATE: | 06-25-2021
DRAWN: | ECL | DIM UNITS: | mm | REVISION: | R00
MATERIAL: | 1/2" ATP-5 AL | FINISH:

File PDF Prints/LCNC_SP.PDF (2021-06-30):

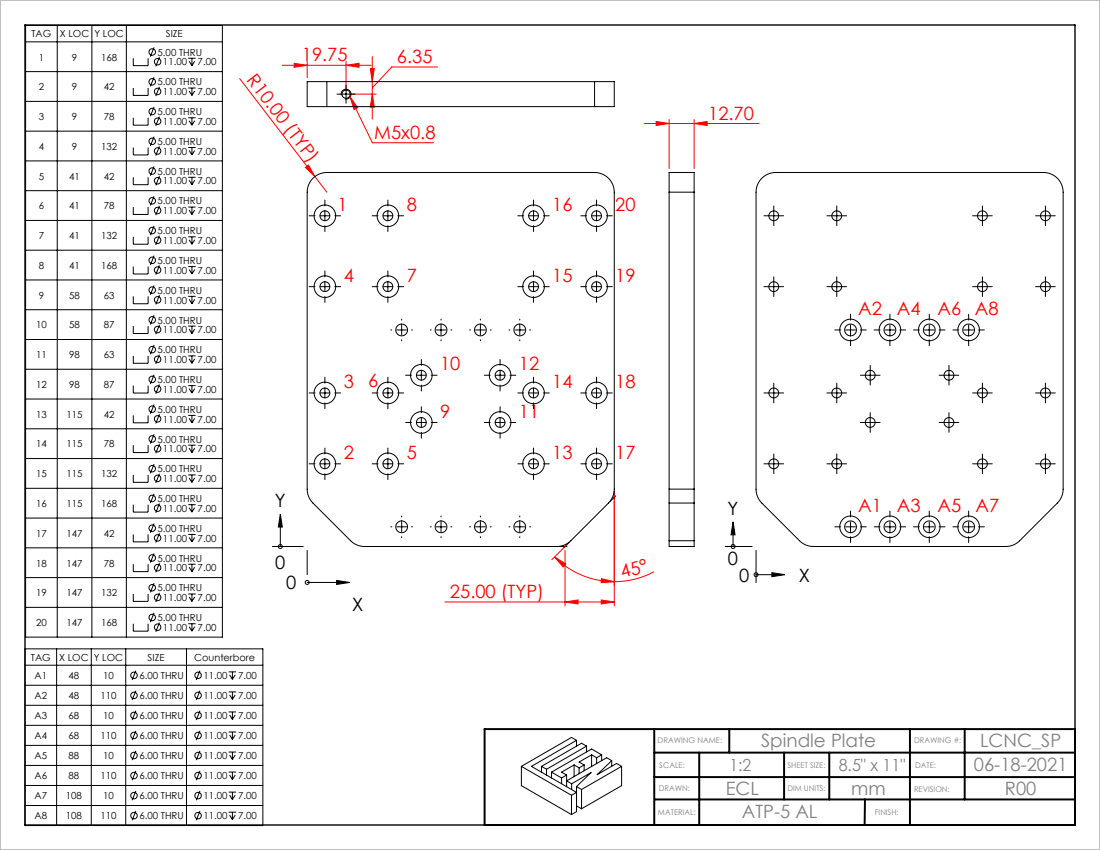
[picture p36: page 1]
R10.00 (TYP); 25.00 (TYP)

TAG | X LOC | Y LOC | SIZE
1 | 9 | 168 | 5.00 THRU

2 | 9 | 42 | 5.00 THRU

3 | 9 | 78 | 5.00 THRU

4 | 9 | 132 | 5.00 THRU

5 | 41 | 42 | 5.00 THRU

6 | 41 | 78 | 5.00 THRU

7 | 41 | 132 | 5.00 THRU

8 | 41 | 168 | 5.00 THRU

9 | 58 | 63 | 5.00 THRU

10 | 58 | 87 | 5.00 THRU

11 | 98 | 63 | 5.00 THRU

12 | 98 | 87 | 5.00 THRU

13 | 115 | 42 | 5.00 THRU

14 | 115 | 78 | 5.00 THRU

15 | 115 | 132 | 5.00 THRU

16 | 115 | 168 | 5.00 THRU

17 | 147 | 42 | 5.00 THRU

18 | 147 | 78 | 5.00 THRU

19 | 147 | 132 | 5.00 THRU

20 | 147 | 168 | 5.00 THRU

TAG | X LOC | Y LOC | SIZE | Counterbore
A1 | 48 | 10 | 6.00 THRU | 11.00 7.00
A2 | 48 | 110 | 6.00 THRU | 11.00 7.00
A3 | 68 | 10 | 6.00 THRU | 11.00 7.00
A4 | 68 | 110 | 6.00 THRU | 11.00 7.00
A5 | 88 | 10 | 6.00 THRU | 11.00 7.00
A6 | 88 | 110 | 6.00 THRU | 11.00 7.00
A7 | 108 | 10 | 6.00 THRU | 11.00 7.00
A8 | 108 | 110 | 6.00 THRU | 11.00 7.00

DRAWING NAME: | Spindle Plate | DRAWING #: | LCNC_SP
SCALE: | 1:2 | SHEET SIZE: | 8.5" x 11" | DATE: | 06-18-2021
DRAWN: | ECL | DIM UNITS: | mm | REVISION: | R00
MATERIAL: | ATP-5 AL | FINISH:

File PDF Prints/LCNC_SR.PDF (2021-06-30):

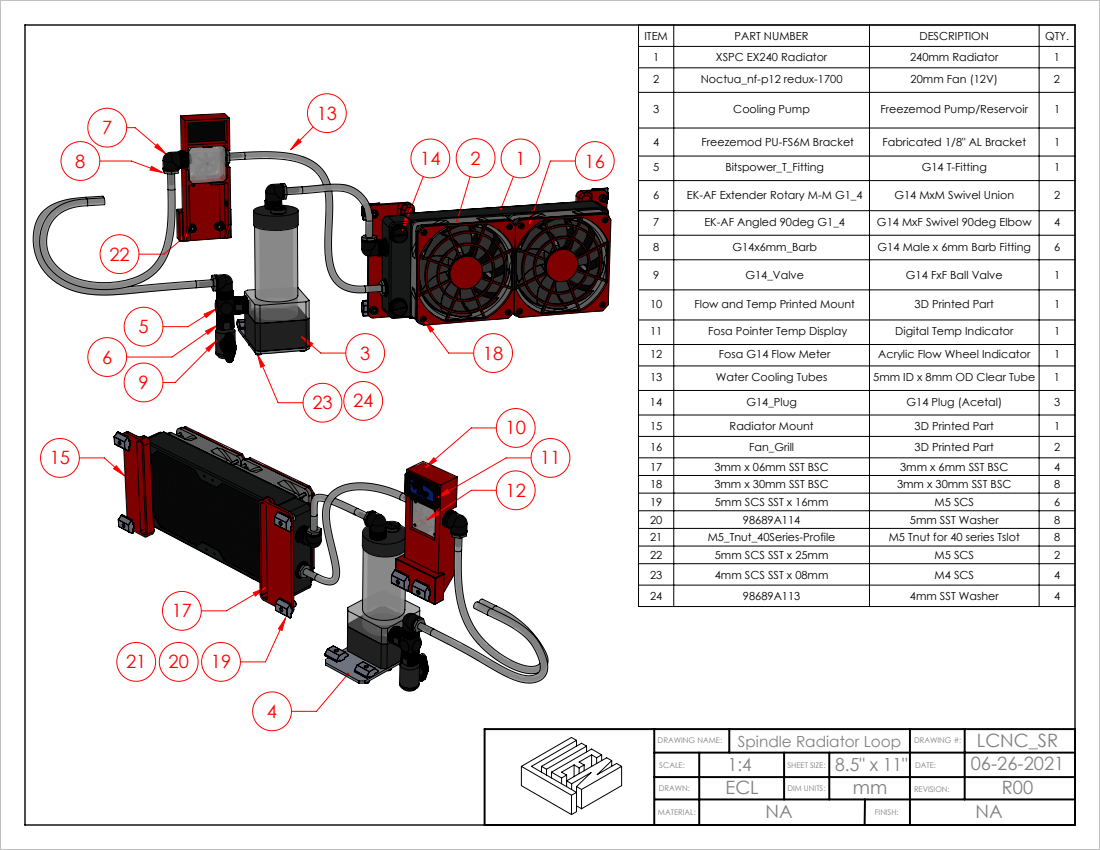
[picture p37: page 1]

ITEM | PART NUMBER | DESCRIPTION | QTY.
1 | XSPC EX240 Radiator | 240mm Radiator | 1
2 | Noctua_nf-p12 redux-1700 | 20mm Fan (12V) | 2

3 | Cooling Pump | Freezemod Pump/Reservoir | 1

4 | Freezemod PU-FS6M Bracket | Fabricated 1/8" AL Bracket | 1
5 | Bitspower_T_Fitting | G14 T-Fitting | 1
6 | EK-AF Extender Rotary M-M G1_4 | G14 MxM Swivel Union | 2
7 | EK-AF Angled 90deg G1_4 | G14 MxF Swivel 90deg Elbow | 4
8 | G14x6mm_Barb | G14 Male x 6mm Barb Fitting | 6
9 | G14_Valve | G14 FxF Ball Valve | 1

10 | Flow and Temp Printed Mount | 3D Printed Part | 1
11 | Fosa Pointer Temp Display | Digital Temp Indicator | 1
12 | Fosa G14 Flow Meter | Acrylic Flow Wheel Indicator | 1
13 | Water Cooling Tubes | 5mm ID x 8mm OD Clear Tube | 1
14 | G14_Plug | G14 Plug (Acetal) | 3
15 | Radiator Mount | 3D Printed Part | 1
16 | Fan_Grill | 3D Printed Part | 2
17 | 3mm x 06mm SST BSC | 3mm x 6mm SST BSC | 4
18 | 3mm x 30mm SST BSC | 3mm x 30mm SST BSC | 8
19 | 5mm SCS SST x 16mm | M5 SCS | 6
20 | 98689A114 | 5mm SST Washer | 8
21 | M5_Tnut_40Series-Profile | M5 Tnut for 40 series Tslot | 8
22 | 5mm SCS SST x 25mm | M5 SCS | 2
23 | 4mm SCS SST x 08mm | M4 SCS | 4
24 | 98689A113 | 4mm SST Washer | 4

DRAWING NAME: | Spindle Radiator Loop | DRAWING #: | LCNC_SR
SCALE: | 1:4 | SHEET SIZE: | 8.5" x 11" | DATE: | 06-26-2021
DRAWN: | ECL | DIM UNITS: | mm | REVISION: | R00
MATERIAL: | NA | FINISH: | NA

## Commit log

2021-06-30 Initial Upload of LienCNC V2
    This is the initial upload of my model and design files for my new CNC Router Project called LienCNC V2. I am sure there will be updates and changes, but it feels good to get the initial release out 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
    [0.25in 18-8 STAINLESS STEEL FLAT WASHER.SLDPRT, 0.25in x 1.125in SST Lag Screw.SLDPRT, 0.375_Nylock.SLDPRT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]
2021-07-01 Added STL's, Split Solidworks Pack-N-Go into sub 100mb files, Added Render
    Added STL's, Split Solidworks Pack-N-Go into sub 100mb files, Added Render
    [Ballscrew Nut Tool.SLDPRT, Ballscrew Nut Tool.STL, CNCDrive_Parts_Mount.STL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]
2021-07-05 Updated BOM and added PDF Version
    It was noticed that I had the wrong number of linear rails and ball screw. That has been corrected and some notes on the BOM. It was also noted that I did not include the cost of the ATP-5 plates. I have added in the raw materials for the aluminum for fabricated parts that I was missing. If someone wanted to build the design they would still need to fabricate the plates which is one of the biggest hurdles to being able to make this machine. I know this, but it is limitation to any DIY from scratch machine.
    I want to thank people for pointing out these issues and missing information. I want this design to be as comprehensive as possible. Again I don't expect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
    [LienCNC_V2 BOM.xlsx]
2021-07-08 Nested Machined Parts Assembly and Nested Prints
    Added better prints for nested machined parts, also added nested parts to other CAD formats for people to import into the CAM packages of their choice.
    [LCNC_NP.DWG, LCNC_NP.DXF, LCNC_NP.SLDDRW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]
